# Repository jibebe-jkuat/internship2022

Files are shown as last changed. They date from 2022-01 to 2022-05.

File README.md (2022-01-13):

# EV project internship 2022

[PPT Slide](https://docs.google.com/presentation/d/1OYJdxiVj7QEA71lRJihHxvrTG2KooOGciBFLIxmFiqk/edit?usp=sharing)
(https://docs.google.com/presentation/d/1OYJdxiVj7QEA71lRJihHxvrTG2KooOGciBFLIxmFiqk/edit?usp=sharing)

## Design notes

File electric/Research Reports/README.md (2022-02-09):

# Contents

**1. Choice of Battery and Motor for Tricycle** - This document focuses on the calculations and
specifications used in determinig the final choice of the motor <br>

**2. Tractor Motor Sizing** - This document focuses on the calculations required for motor to be
used in the Shujaa Tractor. <br>

**3. Torque Calculations** -  This document focuses on the calculations required for torque required
 in the Shujaa Tractor.

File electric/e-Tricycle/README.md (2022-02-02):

# System Specifications

# MOTOR
Motor: BLDC <BR>
Voltage: 48V <br>
Power rating: 1200W <br>
Serial No: TP48V 1200W H60 210918 0001 <br>

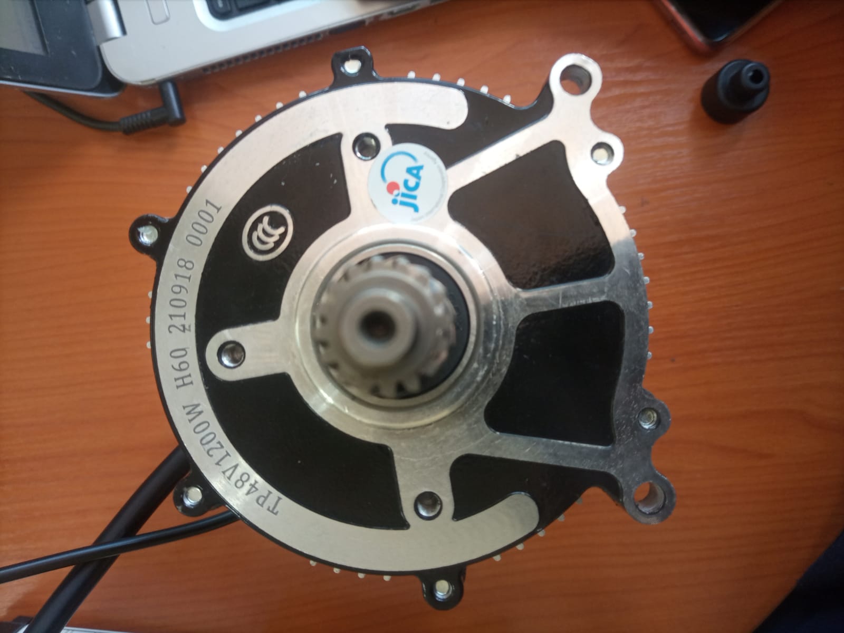
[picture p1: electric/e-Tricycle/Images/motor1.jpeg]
Motor 1

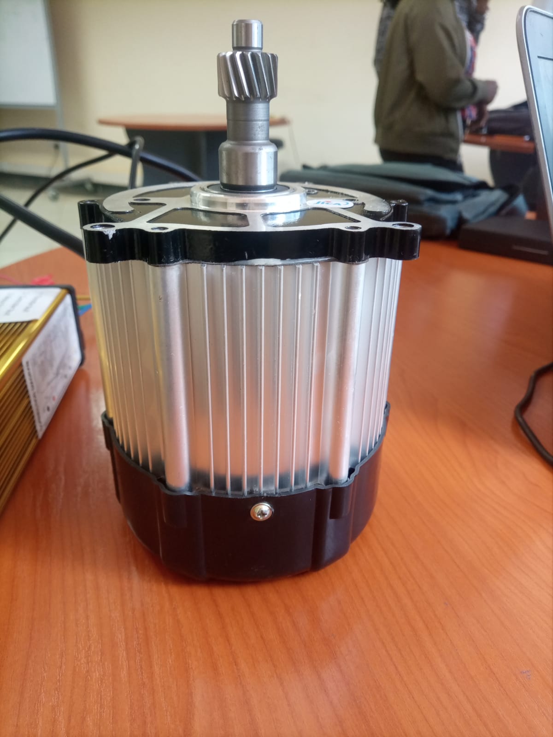
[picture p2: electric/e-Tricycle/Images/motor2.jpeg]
Motor 2


# Speed Controller

Voltage : 48V
Power rating: 1200W

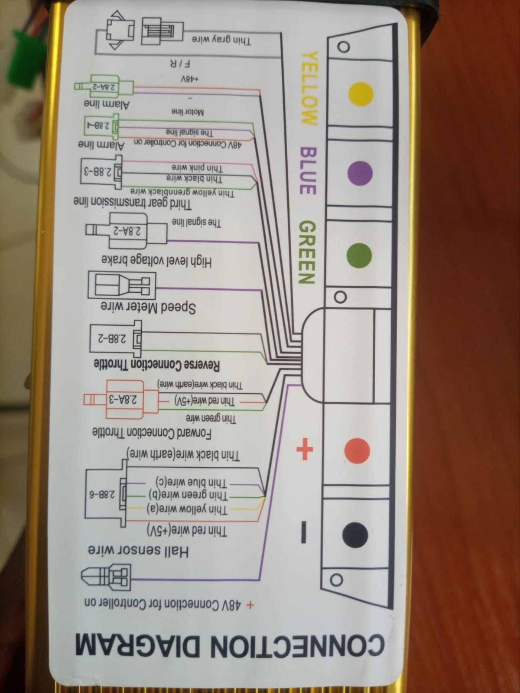
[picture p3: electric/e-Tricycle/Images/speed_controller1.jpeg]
Speed Controller 1

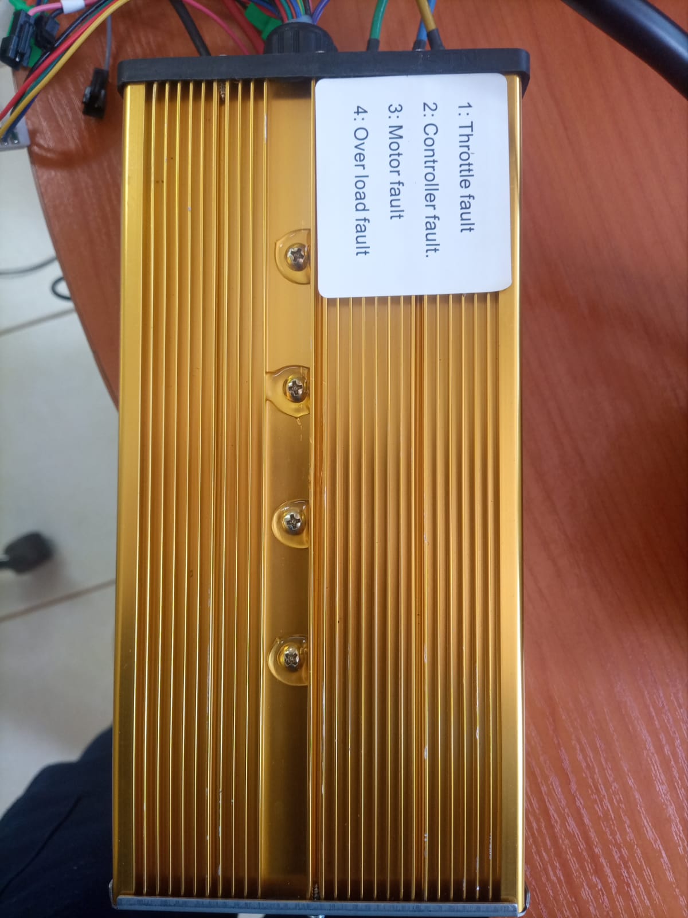
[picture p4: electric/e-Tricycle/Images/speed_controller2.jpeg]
Speed Controller 2

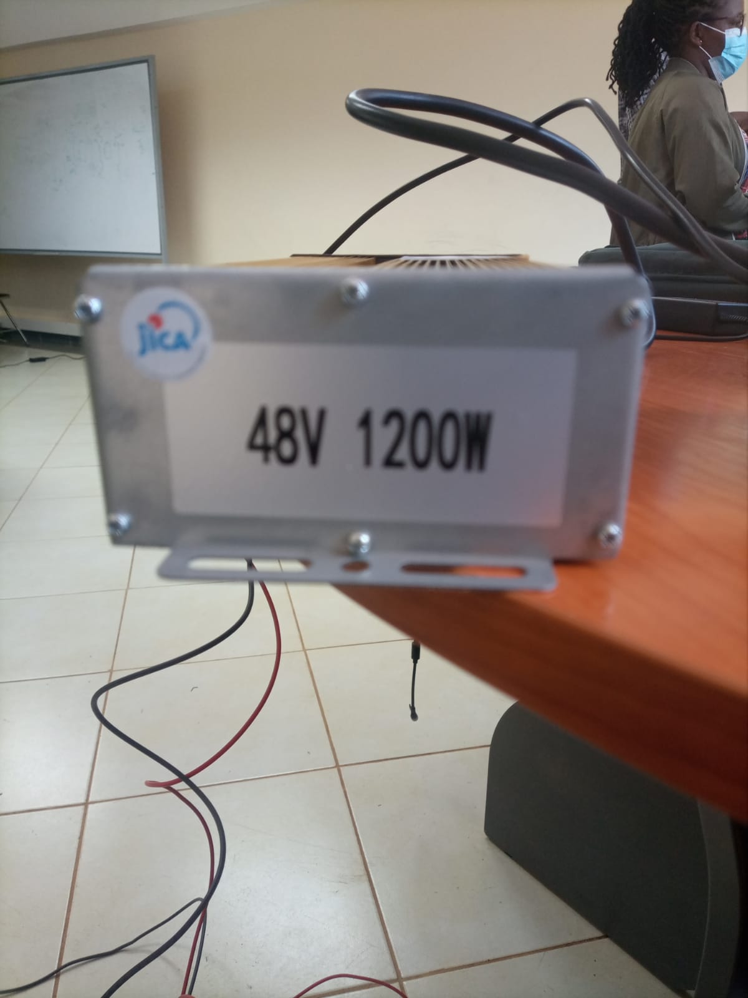
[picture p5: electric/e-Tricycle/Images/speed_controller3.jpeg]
Speed Controller 3

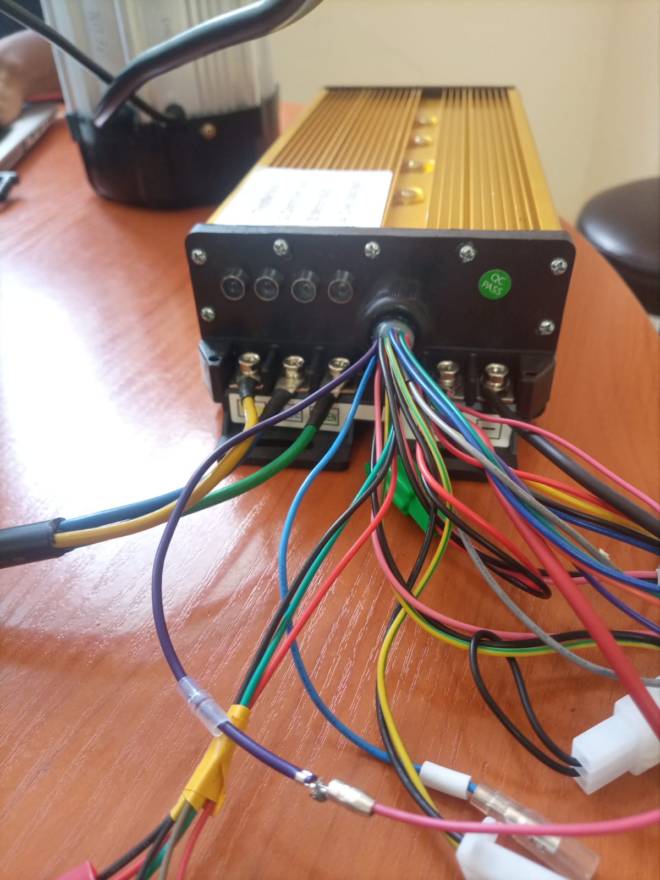
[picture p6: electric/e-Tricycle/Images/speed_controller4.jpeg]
Speed Controller 4


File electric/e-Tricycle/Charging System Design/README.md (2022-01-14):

## Charging System Design

Handles the design of a system to recharge batteries used in the tricycle and the shujaa tractor.

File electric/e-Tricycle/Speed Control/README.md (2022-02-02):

## Speed Control

Involves design of mechanisms to allow for control of the speed of the motor.
Schematics and final designs handled here.

## Design
In this implementation we will control the brushless motor using Arduino and ESC.

## Components

Brushless Motor <br>
ESC 30A <br>
Li-Po battery <br>
Arduino Board <br>
Potentiometer <br>
Breadboard and Jump Wires<br>

## Schematic
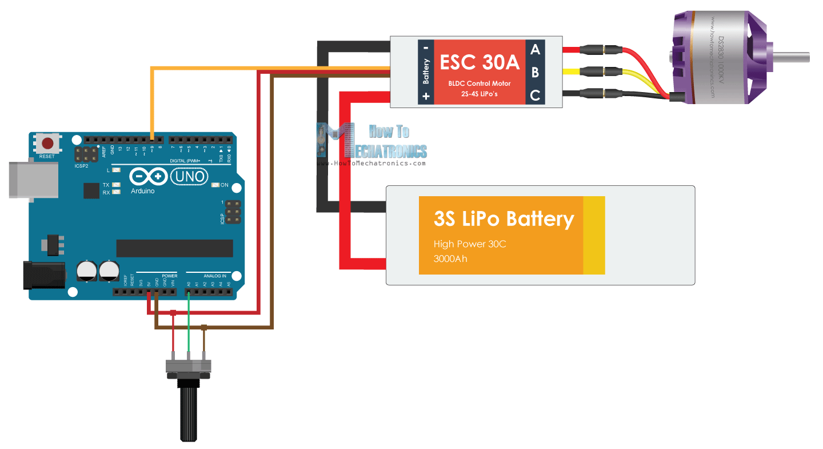
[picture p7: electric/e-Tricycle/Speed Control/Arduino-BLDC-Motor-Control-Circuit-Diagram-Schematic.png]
Circuit Schematic


# Alternative solution
This involves the use of a ready made Handlebar Throttle Switch to allow for the control of speed.

## Reasons for choosing this solution
Pairs well with the motor controller being used.( A plug and play solution). <br>
Has inbuilt LED speed display eliminating the need of an external LCD display. <br>
Does not involve the use of a microcontroller thus saving costs..

## Images of the Handlebar Throttle Switch
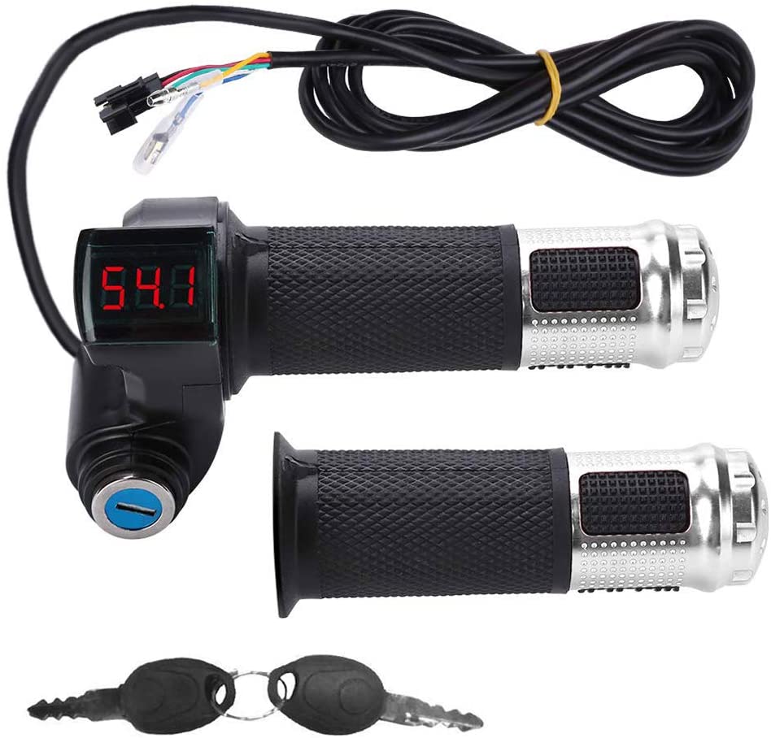
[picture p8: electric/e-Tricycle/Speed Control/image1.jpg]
Throttle Image 1

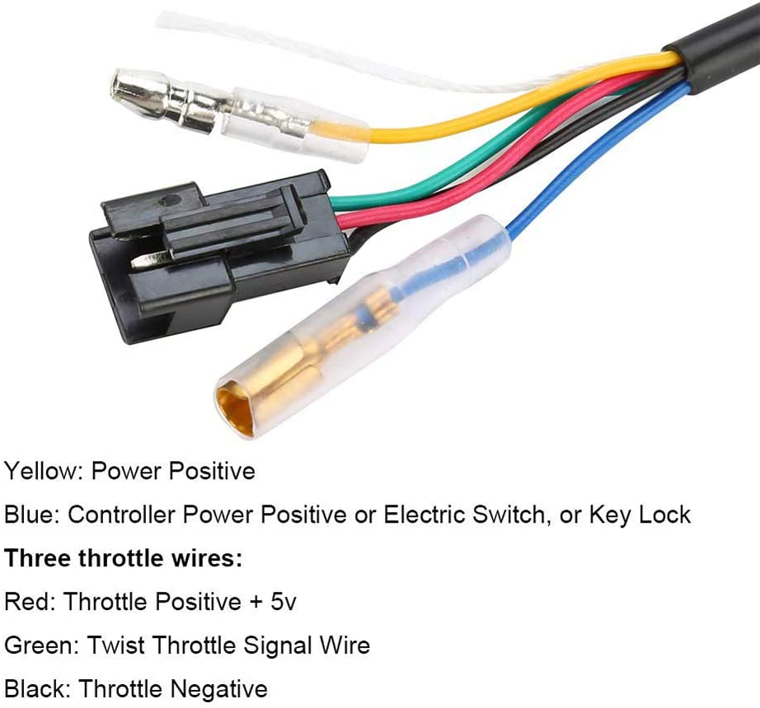
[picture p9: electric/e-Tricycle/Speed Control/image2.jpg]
Throttle Image 2

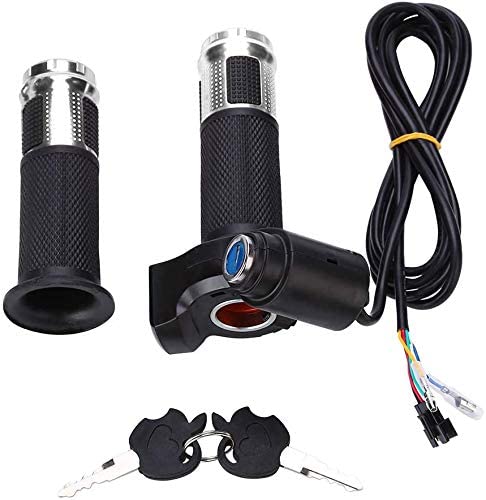
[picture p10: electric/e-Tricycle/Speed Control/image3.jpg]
Throttle Image 3


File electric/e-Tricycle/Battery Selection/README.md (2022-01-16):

## Handles the selection of the battery to be used for the tricycle.

Comparison of various types of batteries is done here.
The calculations and criteria for selection are also defined here.

## Specifications

| Specification | Value |
| --- | --- |
| Mass of motor | |
| Maximum passenger mass  |  |
| Mass of vehicle  |  |
| Mass of batteries |  |
| Total mass |  |
| Motor | BLDC |
| Voltage rating of motor  | 48V  |
| Power rating of motor  | 1800W  |
| Desired range | 100Km |
| Desired top speed | 35 km/h  |

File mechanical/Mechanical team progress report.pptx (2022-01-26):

## Internship 2022 Progress report on E-tricycle Name: Brian Muindi

## Internship 2022 Progress report on E-tricycle Name: Brian Muindi

## Tasks completed last week

- [#Github issue 11]Mechanism for starting motor

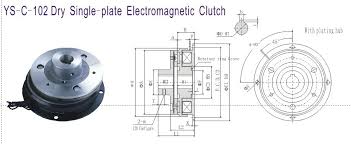
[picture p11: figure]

Why select the electromagnetic clutch?
- High precision torque control
- Superior durability and long life
- Stable slip torque

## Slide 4

- [#Github issue 19]3D modelling of the tricycle

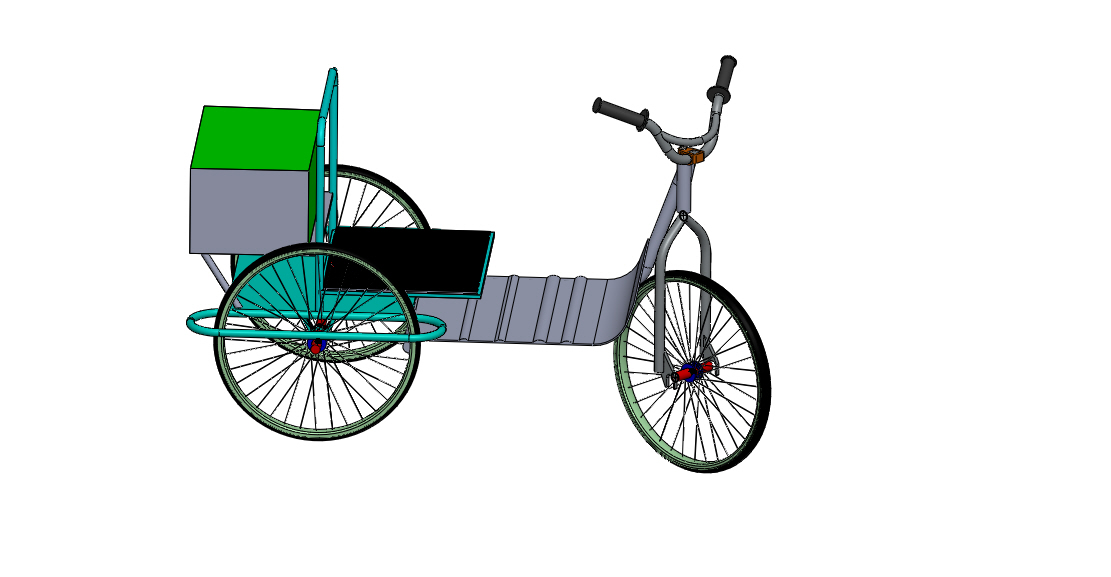
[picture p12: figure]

Parts redesigned
- Steering
- Braking mechanism
- Rear wheels
- Motor positioning

## Tasks in this week

- [#Github issue number 20] Shaft design

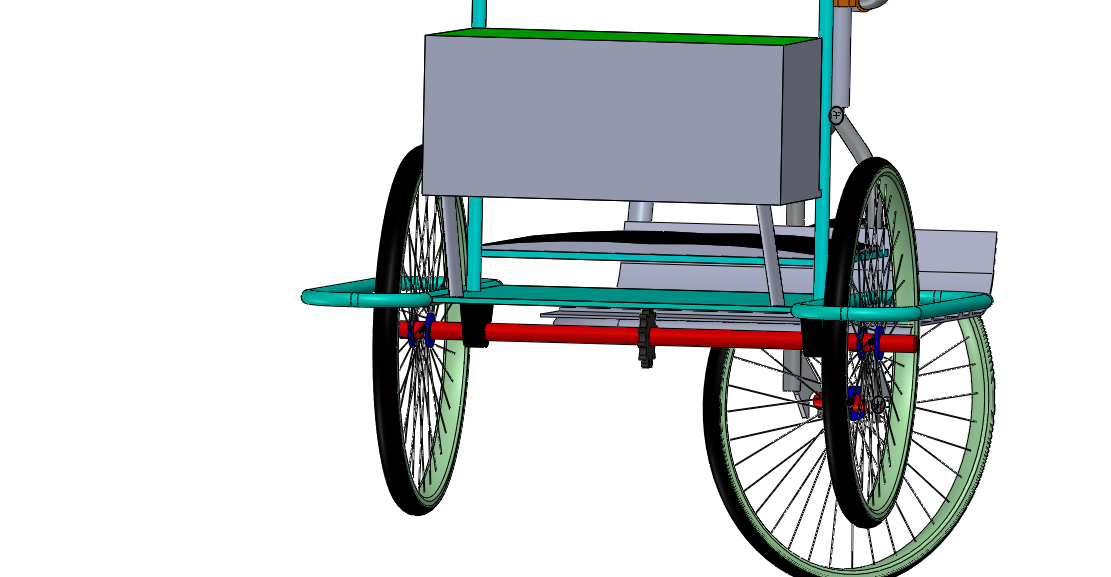
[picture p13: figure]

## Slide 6

- [#Github issue number 21] Design of chain drive

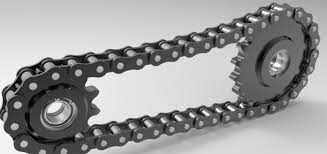
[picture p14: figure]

- No of teeth on sprockets
- Length of chain

## Timeline

Month | Intern week | Tasks
Jan
| Week 1 | Taking measurements and 3D modelling of the tricycle Mechanism for starting the motor Identification of parts
| Week 2 | Design of chain drive Shaft design Acquisition of parts
| Week 3
Feb | Week 4
| Week 5
| Week 6
| Week 7

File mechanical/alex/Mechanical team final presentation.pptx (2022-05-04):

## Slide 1

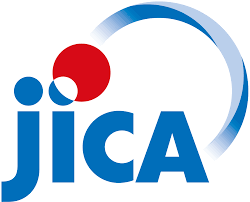
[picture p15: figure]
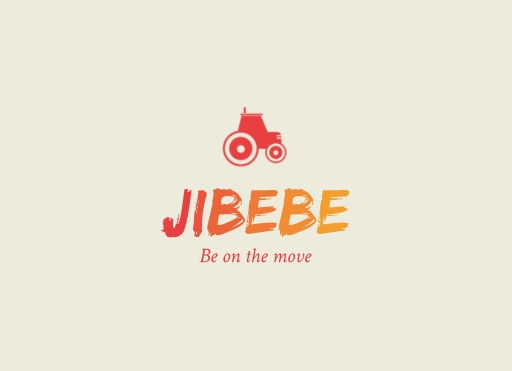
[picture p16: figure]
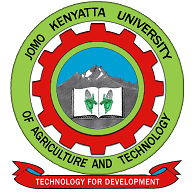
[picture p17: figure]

JIBEBE:ELECTRIC VEHICLE PROJECT

Supervisors : Dr Shohei Aoki
Mr Kipkorir Rono
Mr Joseph Kimani

Mechanical Team

Alex Mburu

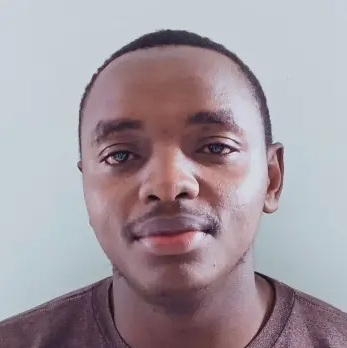
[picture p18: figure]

Emmanuel Njenga

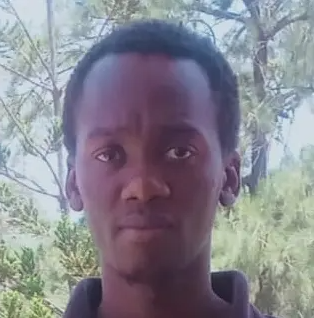
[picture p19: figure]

Peter Nzioki

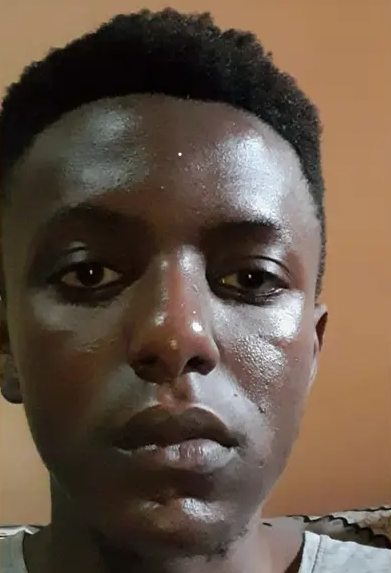
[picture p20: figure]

Brian Muindi

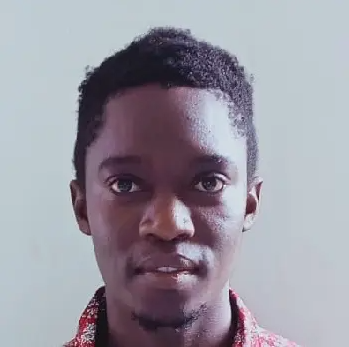
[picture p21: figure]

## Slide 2

INTRODUCTION

HUMAN POWERED TRICYCLE

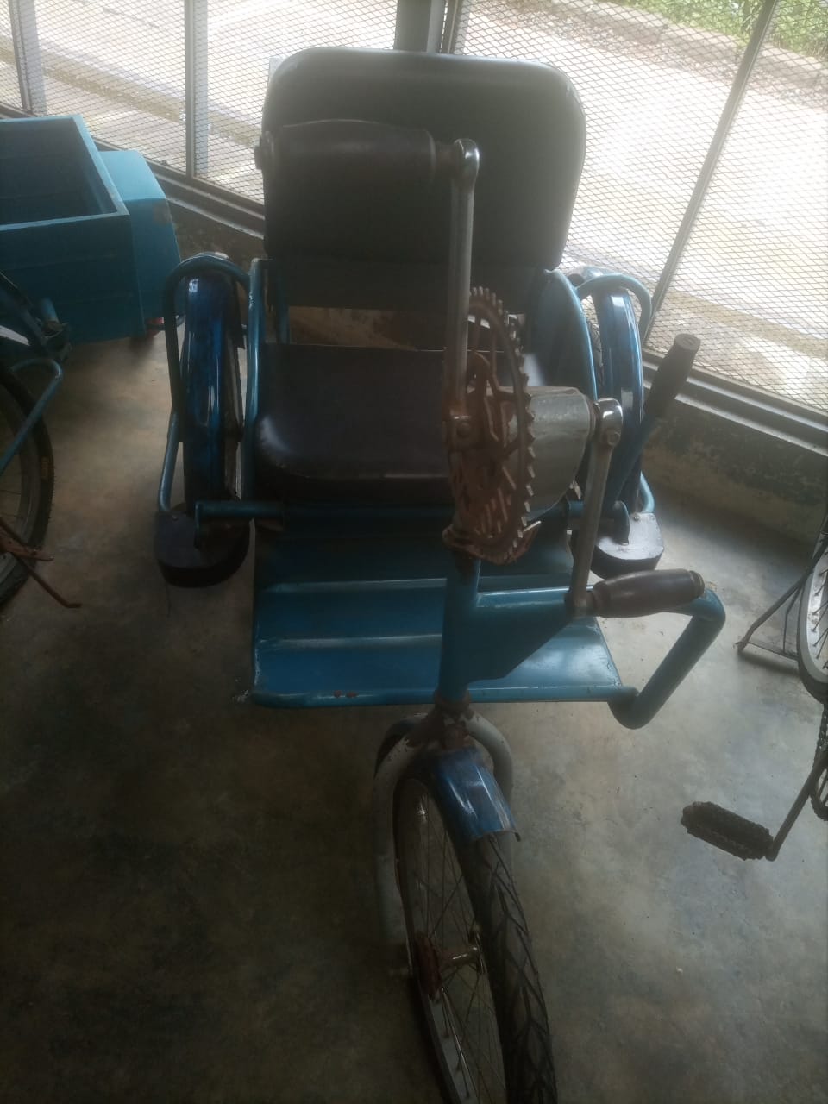
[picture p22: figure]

Specifications
- Human powered tricycle
- Rubber brake shoes-operated by a brake lever

Limitations
- Tedious
- Ineffective brake system

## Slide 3

E-Tricycle

Main Objective
Design fabrication and testing of an electric tricycle
Specific objectives
i. Determine the power requirements for the e-tricycle
ii. Design and fabricate the drive train
iii. Implement mechanical disc brakes

## Key Content Activities

- Power requirements-max speed of 16km/h-1200W-BLDC Motor
- Drive train

Design of rear axle
At 600rpm for the 1200W , T_(max) =19.10Nm
Using the maximum shear stress theory (Guest’s theory)
√(M^2 +T^2) = π/16×τ_(max) ×d^3
Diameter= 15.62mm

Chain drive design
- Design for the sprockets
Speed ratio=3.5
The larger sprocket=47T
Smaller sprocket = 15T
- Design for the chain
D=180mm
d=70mm
Center distance ,x = 170mm
Chain length= π(R+r)+2x+((R−r)/X)^2
L=760mm

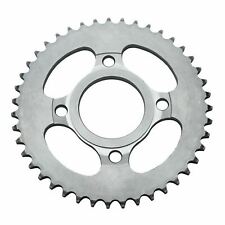
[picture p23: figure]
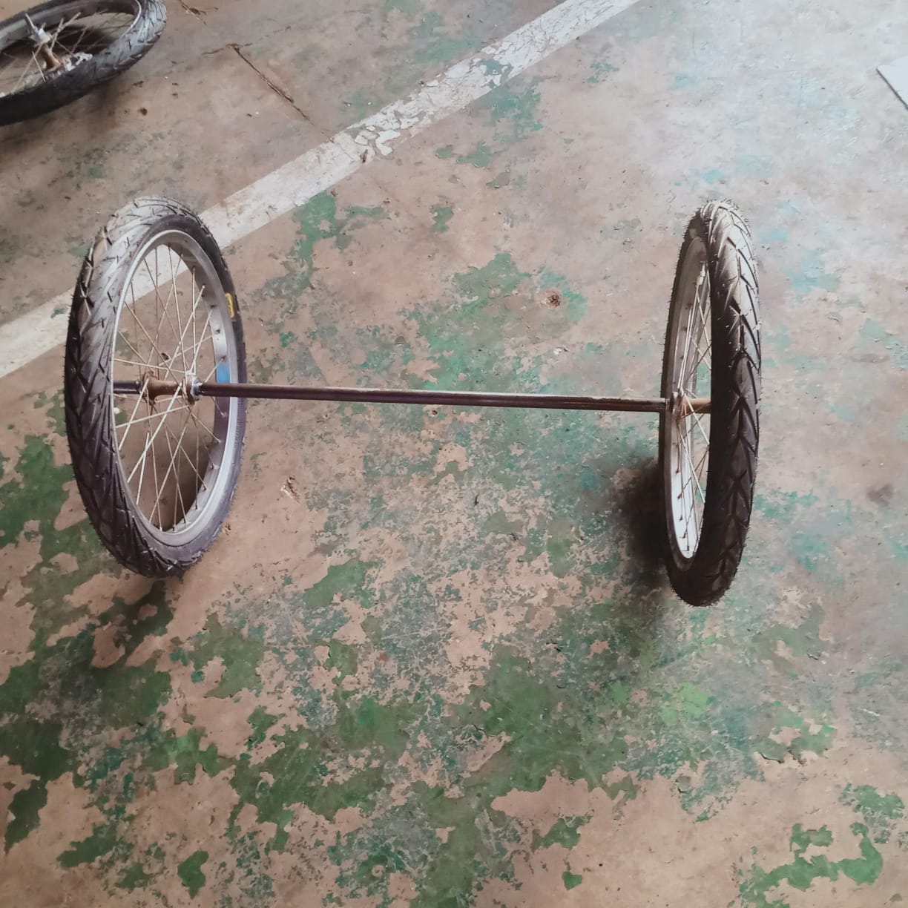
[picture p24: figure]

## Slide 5

3D modeling of the tricycle


Parts redesigned
- Steering
- Braking mechanism
- Rear wheels
- Motor positioning

Motor

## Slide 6

Fabrication and assembly of components

1.Steering-handle bars –
easy steering and other attachments i.e throttle,brake shifters

2.Braking mechanism
Mechanical brakes-both front and rear


Brake shifters


Rear Brake
rotor


Brake calipers

Front Brake
rotor

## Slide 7

Large sprocket

Drive train


BLDC motor

Chain


Motor


Attachment on the motor


Chain

Sprocket

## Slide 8

Assembly and testing of the e-tricycle

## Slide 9

Recommendations

1. Implement a suspension system for better ride comfort
2. Centre alignment of the handle bars to improve steering and better handling

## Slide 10

E-TRACTOR

Main Objective
Design fabrication and testing of an electric tractor
Specific objectives
i. Determine the power requirements for the e-shujaa tractor
ii. Stress and vibrational analysis of the e-tractor chassis
iii. Redesign the transmission system
iv. Assembly and testing of the e-tractor

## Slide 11

POWER REQUIREMENTS FOR THE SHUJAA E-TRACTOR

Case 1:Working mode
Power required when the tractor is accelerating(0-11km/h) and ploughing= 6.7923 kw

Case 2:Transport mode
Power required when the tractor is accelerating(0-30km/h) but NOT ploughing= 6.855kW

TORQUE REQUIREMENTS FOR THE SHUJAA E-TRACTOR

Case 1:Working mode
Working speed=11km/h
Torque from motor=27.28Nm
Torque required at the driving wheels=1800Nm

Gear ratio=47.98

Case 2:Transport mode
Working speed=30km/h
Torque from motor=27.28Nm
Torque required at the driving wheels=479.98Nm

15kW motor

Gear ratio=17.59

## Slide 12

Static and vibration analysis of the tractor chassis

Static analysis


Frequency analysis

Freq No | Rad/sec | Hertz
1 | 2986.7 | 475.34
2 | 5540.9 | 881.86
3 | 11383 | 1811.7
4 | 13137 | 2090.9
5 | 13327 | 2121.1

For a top speed of 3500rpm
Operating frequency of the motor is 58.33Hz (366.52rad/s)

FOS=15

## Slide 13

Thank you


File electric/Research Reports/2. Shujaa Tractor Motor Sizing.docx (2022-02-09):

JIBEBE

ELECTRICAL SUBSYSTEM

# MOTOR SIZING Calculations for Shujaa Tractor Motor

___

Placeholder image

# INTRODUCTION

This document will focus on the sizing of the motor to be used for the Shujaa Tractor. Proper sizing of a motor requires that 3 criteria must be met: torque, load inertia, and speed.

## A. Considering Tilling only

## Torque

This is defined as rotational force at a distance from the rotational axis. It is measured by units such as lb-in (pounds inch) in imperial or Nm (newton meter) in metric. Torque is just as important, if not more important, than the horsepower of a motor. Horsepower is how fast the work can be done and is calculated with torque multiplied by speed. In other words, torque is the capacity to do the work, and power is the speed at which the work can be done.

## Load Torque

Torque has 2 main components: load torque and acceleration torque. Load torque is the amount of torque constantly required for application and includes friction load and gravitational load. Acceleration torque is the torque required just for the maximum acceleration and deceleration rate for the load. The faster the load needs to accelerate, the higher the acceleration torque is. Sometimes the load torque is higher; sometimes the acceleration torque could be higher.

### 1. Lorem ipsum

Lorem ipsum dolor sit amet, consectetuer adipiscing elit, sed diam nonummy nibh euismod tincidunt ut laoreet dolore magna aliquam erat volutpat. Ut wisi enim ad minim veniam, quis nostrud exerci tation ullamcorper suscipit lobortis nisl ut aliquip ex ea commodo consequat.

### 2. Dolor sit amet

Duis autem vel eum iriure dolor in hendrerit in vulputate velit esse molestie consequat, vel illum dolore eu feugiat nulla facilisis at vero eros et accumsan.

## B. Considering Movement only

.For deciding the power rating of a vehicle, the vehicle dynamics like rolling resistance, gradient resistance, aerodynamic drag, etc. have to be considered. For illustration procedure for selecting

motor rating for an electric car of gross weight 450 kg is considered.

The force required for driving a vehicle is calculated below [1]-[4]:

Ftotal=Frolling+Fgradient+Faerodynamic drag (1)

Where, Ftotal =Total force

Frolling= force due to Rolling Resistance

Fgradient resistance= force due to Gradient Resistance

Faerodynamic drag=force due to aerodynamic drag

Ftotal is the total tractive force that the output of motor must overcome, in order to move the vehicle.

### A. ROLLING RESISTANCE

Rolling resistance is the resistance offered to the vehicle due to the contact of tires with road. The formula for calculating force due to rolling resistance is given by equation (2):

Frolling=Crr*M*g (2)

Where, Crr= coefficient of rolling resistance

M= mass in kg

g= acceleration due to gravity= 9.81 m/s²

Reference for Crr

Car tire on concrete: 0.010 to 0.015 , Steel on steel: 0.02 , Steel on wood: 0.22

Car tire on tar or asphalt: 0.030 to 0.035 , Aluminum on steel: 0.10 to 0.15

For the application considered, i.e a farm , choose rolling resistance to be 0.09 .

This paper (https://www.cambridge.org/core/services/aop-cambridge-core/content/view/ECD7544F00543D596B2D0EB3DD639516/S2633776220000758a.pdf/rolling-resistance-of-atv-tyre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) has values for rolling resistance in agriculture.

Crr=0.09 M= 450 kg, g = 9.81

Therefore,

Frolling= Crr*M*g

Power required to overcome the rolling resistance is:

Prolling= Frolling*V/3600 (3)

Where, V=velocity in kmph.

### B. GRADIENT RESISTANCE

Gradient resistance of the vehicle is the resistance offered to the vehicle while climbing a hill or flyover or while travelling in a downward slope.

The angle between the ground and slope of the path is represented as α, which is shown in the Figure below.


Figure: Angle between the ground and slope of a path

The formula for calculating the gradient resistance is given by equation (4):

Fgradient resistance=+ M*g*sin α (4)

In this illustration, let us consider the electric tractor runs on a flat road. Therefore, the angle α =0⁰

### C. AERODYNAMIC DRAG

Aerodynamic drag is the resistive force offered due to viscous force acting on the vehicle. It is largely determined by the shape of the vehicle.

The formula for ca lculating the aerodynamic drag is given by equation (5):

Faerodynamic drag= 0.5*CA*Af*ρ*(V+Vo)² (5)

These are the three main forces which act on the vehicle when it travels at constant speed. While accelerating and decelerating the effect of force due to inertia also acts. In this section, let us consider the power required to overcome Aerodynamic drag and other resistive forces to be around 1.3 kW.

### D. EFFIENCY

The total Power can then be calculated from the addition of the three powers above.

But electric motor with output power rating above should not be selected. The losses due transmission of power to the wheel must be included.

Therefore, the mechanical power output (Mtractive) required to drive the vehicle is given by equation (6):

Mtractive = Ptotal / η (6)

Where, η= efficiency of the transmission gear system.

Let us consider the efficiency of the transmission system to be 0.85.

Therefore the mechanical power output required can be calculated and appropriate motor can be selected.

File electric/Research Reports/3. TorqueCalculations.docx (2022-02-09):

Calculations To Determine The Maximum Torque To Be Produced By The Motor

The expected maximum load given acceleration of 0.5m/s² and a carriage of 220Kg is is 500W. To determine the maximum torque required for this application, then:

P=τω

ω=(2πn)/60

Smaller Sprocket: 48.42mm

Larger sprocket: 17.5cm

Wheel: 50cm

C = 2πr = πd

Diameter of wheel = 0.5m

Cof wheel = π x 0.5=0.5π m

Distance (D) covered by the wheel is 0.5π m/rev

The maximum speed of the tricycle is 4.5 m/s

Therefore, to obtain the number of revolutions per second for the wheel at maximum speed:

Speed in rps = ((4.5m)/s)/(0⋅5πm/(rⅇv))=9/π rev/s = 9/πrps

In rpm = 9/π x 60= 540/πrpm= 171.8873385 rpm

Method 1:

Large Sprocket Parameters:

Since angular velocity is the same for two axially connected wheels, then the rpm of the wheel is the same as the rpm of the large sprocket:

Rpm of wheel = 540/πrpm

C = 2πr = πd

Diameter of large sprocket = 0.175m

Cof wheel = π x 0.175m=0.175π m

Distance (D) covered by the larger sprocket is 0.175π m/rev

Linear speed of larger sprocket = 540/πrev/min x 0.175π m/rev = 94.5 m/min = 1.575 m/s

Small Sprocket parameters:

Since linear velocity is the same for two radially connected wheels, then the linear velocity of the large sprocket is the same as the linear velocity of the small sprocket:

V of small sprocket = 1.575 m/s

C = 2πr = πd

Diameter of small sprocket = 0.04842m

Cof small sprocket = π x 0.04842=0.04842π m

Distance (D) covered by the small sprocket is 0.04842π m/rev

Speed in rps = ((1.575m)/s)/(0⋅04842πm/(rⅇv))=8750/(269 π) rev/s = 8750/(269 π)rps

In rpm = = 8750/(269 π) x 60= 621.2367667 rpm

P=τω

ω=(2πn)/60

ω=(2π x 621.2367667)/60=65.05576208 rad/s

τ=P/ω= 500/65.05576208=7.685714286 nm

Method 2:

Large Sprocket Parameters:

Since angular velocity is the same for two axially connected wheels, then the rpm of the wheel is the same as the rpm of the large sprocket:

ω=(2πn)/60

ω=(2π x 540/π)/60

ω=(2πn)/60=18 rad/s

And r of the larger sprocket is 0.0875m

v=rω=0.0875 x 18=1.575 m/s

Small Sprocket parameters:

Since linear velocity is the same for two radially connected wheels, then the linear velocity of the large sprocket is the same as the linear velocity of the small sprocket:

V of small sprocket = 1.575 m/s

Radius = 0.02421m

ω=v/r

ω=1.575/0.02421=65.05576208 rad/s

τ=P/ω= 500/65.05576208=7.685714286 nm

On a flat surface, the expected torque at maximum speed is approximately 8 nm.

However, if the angular velocity was to fall due to motion on an inclined plane, i.e. a ramp, then the torque would dramatically increase. Let us take a critical case where the angular velocity dropped to 5 rad/s.

P=τω

τ=P/ω= 500/5=100 nm

Our BLDC motor is rated for an adjustable maximum torque between 120nm to 320nm hence it is safe above an angular velocity of:

ω=P/τ= 500/320=1.5625 rad/s

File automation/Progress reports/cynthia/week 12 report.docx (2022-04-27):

Internship 2022

# Progress report format for team meeting

Name: CYNTHIA KEMBOI

## Tasks completed last week

- [#83] GPS and Raspberry Pi

The raspberry pi’s OS was configured to be able to communicate with the GPS receiver. The circuit and the data collected are as shown below;


Figure 1 raspberry pi and GPS


Figure 2 data collected


Figure 3 position of our raspberry pi

- [#87] Raspberry Pi and Compass

Magnetometer HMC5883L is used for measuring the direction and magnitude of the Earth’s magnetic field. It is used for low-cost compassing and magnetometry. It measures the Earth’s magnetic field value along the X, Y and Z axes from milli-gauss to 8 gauss. It can be used to find the direction of heading of the device. It uses I2C protocol for communication with microcontroller.

After initialization, X,Y AND Z-axis registers raw values, The head value is calculated using the following formulae:

Magnetic heading=atan2(y/x) (radian)

True heading=Magnetic heading+Declination Angle (Radian)


Figure 4 raspberry pi and compass


Figure 5 compass detected

## Navit

Navit is a car navigation system with routing engine. Navit's modular design is capable of using vector maps of various formats for routing and rendering on the screen. It's even possible to use multiple maps at the same time. The GTK+ or SDL user interfaces are designed to work well with touch screen displays. Points of Interest of various formats are displayed on the map. The current vehicle position is either read from gpsd or directly from NMEA GPS sensors. The routing engine not only calculates an optimal route to your destination, but also generates directions and even speaks to you using espeak. Navit currently speaks 49 languages, can run on various platforms (Linux, Windows, Android, OpenMoko Freerunner, Wince, Nokia n800 Internet tables, iPhone, Zaurus..)

## Tasks in this week

- [#88] Raspberry Pi and Navit

# Timeline

Month | Intern week | Tasks
Jan
| Week 1 | Identification of parts and drawing of the chassis diagram.
| Week 2 | Circuit diagram and acquisition of parts.
| Week 3 | Definition of the path to be followed by the robot car. Laser cutting of the parts.

Feb | Week 4 | - Assembly of the robot - Ultrasonic program implementation
| Week 5 | - GPS and compass navigation - Path definition
| Week 6 | Object identification using computer vision. (Raspberry pi & camera)
| Week 7 | Transmission of live feed and data from the robot (transmitter and receiver)
| Week 8 | Object dection (static and dynamic)

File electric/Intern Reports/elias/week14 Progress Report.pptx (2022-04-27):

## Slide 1

JIBEBE INTERNSHIP 2022


WEEKLY REPORT: ELIAS CHERUIYOT

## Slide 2

[#96] Eliminating inconsistency of motor speeds- The team managed to smoothen out inconsistency of speeds of the motor by introducing a 100uF capacitor on the linear acceleration circuit.
[#97]Incorporating reverse function in e-tricycle- The team managed to come up with a circuit that Incorporating reverse function. Circuit which has
1. Button for reverse direction.
2. Large LED/Industrial LED to indicate reverse is engaged.
3. Buzzer to also indicate reverse is engaged


TASKS COMPLETED LAST WEEK


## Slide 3


## TASKS THIS WEEK

- [#84] PCB drawing and fabrication-

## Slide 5


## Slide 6

Thank You

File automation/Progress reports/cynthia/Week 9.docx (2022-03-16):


Internship 2022 Progress report

Name: Cynthia Kemboi

# Tasks completed last week

- [#71] Tillage and automation.

Development of guidance systems and autonomous vehicles is current state-of-the-art in agricultural mechanization. Since the late nineteenth century, farmers have been devising methods of making a tractor follow a plough furrow by using a feeler. In the later part of the twentieth century, the combination of hydraulics and electronics allowed for more sophisticated guidance strategies. These strategies include low force feelers that can guide the tractor or implement based on the position or rows, and guiding the tractor based on the position of the vehicle from the Global Positioning System (GPS).

Using a guidance system for agricultural machinery is not a new concept. One of the earliest guidance systems used a wheel to steer a steam-powered traction engine along a plow furrow. A small steel wheel was designed to run in a plow furrow next to the tractor. The guidance wheel was attached to the front wheels of the tractor and held up against the furrow using a spring. As the tractor veered left or right, the guidance wheel in the furrow would steer the tractor in the opposite direction, keeping it on track parallel to the plow furrow.


Figure showing an early furrow following guidance system

Depending on the situation, different guidance strategies or groups of guidance strategies may be needed to achieve the best outcome. Each strategy uses or combines various technologies to guide the vehicle. For example, consider a tractor cultivating a row crop, such as cotton. A sensor with feelers can locate the row accurately, and ensure that the vehicle follows the row. However, there is no assurance that the tractor is cultivating the correct set of rows. The GPS system can locate the tractor on the proper set of rows, but the accuracy may not be precise enough to cultivate between the rows without damaging the crop. The two systems may be combined to provide a better solution. The ECU can use the GPS portion of the guidance system to ensure that the tractor is cultivating the correct set of rows then switch to the feeler guidance system to ensure that the cultivator is accurately operating between the rows, minimizing the damage to the crops.


A guidance system that uses crop feelers

There are four guidance strategies:

1. Manual—an operator steers the vehicle based on their observations of the surroundings.
2. Operator assisted—an operator steers the vehicle based on a signal from the guidance system.
3. Semi-autonomous—the guidance system steers the vehicle, but an operator is present to ensure the system is working properly and perform other vehicle functions that are not automated.
4. Fully autonomous—no operator required! The benefits and challenges of each strategy are identified below


# Tasks in this week

● [#49] Computer vision (vehicle detection, static and dynamic objects )

# Timeline

Month | Intern week | Tasks
Jan
| Week 1 | Identification of parts and drawing of the chassis diagram.
| Week 2 | Circuit diagram and acquisition of parts.
| Week 3 | Definition of the path to be followed by the robot car. Laser cutting of the parts.

Feb | Week 4 | - Assembly of the robot - Ultrasonic program implementation
| Week 5 | - GPS and compass navigation - Path definition
| Week 6 | Object identification using computer vision. (Raspberry pi & camera)
| Week 7 | Transmission of live feed and data from the robot (transmitter and receiver)
| Week 8 | Object dection (static and dynamic)

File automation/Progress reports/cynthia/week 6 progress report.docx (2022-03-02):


Internship 2022 Progress report format

Name: CYNTHIA KEMBOI

# Tasks completed last week

## ● [#49] Computer Vision

Computer vision is a field of artificial intelligence (AI) that enables computers and systems to derive meaningful information from digital images, videos and other visual inputs, and take actions or make recommendations based on that information. If AI enables computers to think, computer vision enables them to see, observe and understand.

Computer vision works much the same as human vision, except humans have a head start. Human sight has the advantage of lifetimes of context to train how to tell objects apart, how far away they are, whether they are moving and whether there is something wrong in an image.

Computer vision trains machines to perform these functions, but it has to do it in much less time with cameras, data and algorithms rather than retinas, optic nerves and a visual cortex. Because a system trained to inspect products or watch a production asset can analyze thousands of products or processes a minute, noticing imperceptible defects or issues, it can quickly surpass human capabilities.

Applications

- Intruder detection
- Defect detection
- Metrology
- Assembly verification
- Screen reading
- CV plus robotics for bin picking

Computer vision with the Raspberry Pi

Computer Vision (CV) allows your Raspberry Pi to see things. In practical terms, this means that your Raspberry Pi can analyze an image, looking for items of interest and even recognizing faces and text.

If you link this with a camera to supply the images, then all sorts of possibilities open up.


The raspberry pi-based obstacle avoiding robot consists of three main modules i.e., camera module, raspberry pi, motor drivers. The camera module gets the input image which are obtained during real time operation. The raspberry pi is a platform consisting of all necessary hardware module assembled on it. It receives the images from the camera module. It carries out image processing and checks whether there are any obstacles in path of the robot and if any obstacle occurs then it will send the signal further to motor driver accordingly. The motor driver actually of two sub motors- left and right motor. These motors receive the signal from raspberry pi in case of any appearance if the obstacle in its path the motors work accordingly to signal and moves in left or right direction with the help of the left and right motor to avoid obstacles.


There are two versions of the Camera Module:

- The standard version (https://www.raspberrypi.org/products/camera-module-v2/), which is designed to take pictures in normal light
- The NoIR version, which doesn’t have an infrared filter, so you can use it together with an infrared light source to take pictures in the dark

# Tasks in this week

- [#50] object detection and identification
- [#51] raspberry pi and Arduino mega connection
- [#26] obstacle avoidance using computer vision

# Timeline

Month | Intern week | Tasks
Jan
| Week 1 | Identification of parts and drawing of the chassis diagram.
| Week 2 | Circuit diagram and acquisition of parts.
| Week 3 | Definition of the path to be followed by the robot car. Laser cutting of the parts.

Feb | Week 4 | - Assembly of the robot - Ultrasonic program implementation
| Week 5 | - GPS and compass navigation - Path definition


| Week 6 | Object identification using computer vision. (Raspberry pi & camera)
| Week 7 | Transmission of live feed and data from the robot (transmitter and receiver)
| Week 8 | Implementation of tillage program on the robot (gathering and casting).

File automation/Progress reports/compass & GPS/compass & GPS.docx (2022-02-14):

Compass

The HMC5883L sensor is a 3-axis digital magnetometer IC designed for low-field magnetic sensing. The sensor has a full-scale range of +8 to -8 Gauss and a resolution of up to 5 milli-Gauss. Communication with the HMC5883L is simple and all done through an I2C interface. That means you will need to connect power, ground and only two cables to Arduino Uno board (SDA, SCL).

The HMC5883L board can be powered up by 5V or 3.3V pins of Arduino Uno board. No need to add any capacitors or resistors to your circuit.

Pinout and connection with Uno:

- Vcc to 5V or 3.3V
- GND to GND
- SDA to A4
- SCL to A5
- DRDY to nothing...

Because this is a magnetic compass if you put it near to battery, motors, metallic surface or magnetic field, the result will diverge from the actual.

The HMC5883L utilizes Anisotropic Magneto resistive (AMR) technology that provides advantages over other magnetic sensor technologies. These anisotropic, directional sensors feature precision in-axis sensitivity and linearity. These sensors’ solid-state construction with very low cross-axis sensitivity is designed to measure both the direction and the magnitude of Earth’s magnetic fields, from milli-gauss to 8 gausses.


GPS

The Global Positioning System (GPS) is a satellite based navigation system that provides location and time information. The system is freely accessible to anyone with a GPS receiver and unobstructed line of sight to at least four of GPS satellites. A GPS receiver calculates its position by precisely timing the signals sent by GPS satellites.

GPS modules contain tiny processors and antennas that directly receive data sent by satellites through dedicated RF frequencies. From there, it’ll receive timestamp from each visible satellites, along with other pieces of data. If the module’s antenna can spot 4 or more satellites, it’s able to accurately calculate its position and time.

The four well-known Global Navigation Satellite System include GPS, BDS(Beidou), GLONASS and GALILEO four satellite navigation systems. The earliest appeared in the United States is GPS (Global Positioning System), which is the most complete technology at this stage. BDS, GLONASS and GALILEO have become the other largest satellite navigation systems in the world and are currently in the process of modernization.


Figure 1 satellite triangulation


Figure 2 GPS Expectations

The first stage of the autonomous guidance algorithm determined the angle difference by comparing the current heading to the target azimuth. This step allowed the robot to determine what direction (left or right) it should turn. The next step determined the distance between the robot location and the target location. The robot program continuously calculates the distance and the minimum turn required. When the heading angle is equal to the azimuth angle, the robot is steered towards the destination point. When the distance is equal to zero, the robot arrives at the destination point


Figure 3 Autonomous robot guidance algorithm

A waypoint is the term used to describe a reference point for robot navigation. It includes destination latitude and longitude data. In this study, waypoints stored previously in the database were used for point-to-point steering in autonomous robot guidance. Two important angles called heading and azimuth angles were used to steer the robot autonomously. The heading angle was an angle between North (true or magnetic) and the current direction of the longitudinal axis of a robot in the horizontal plane. It was continuously received from the GPS receiver by the robot program. The azimuth was an angle between North and the destination point. It was continuously calculated by the robot program with Harvesine equation.

The Haversine formula calculates the shortest distance between two points on a sphere using their latitudes and longitudes measured along the surface. It is important for use in navigation.

The haversine can be expressed in trigonometric function as:

haversine(θ)=sin^2 θ/2 The haversine of the central angle (which is d/r) is calculated by the following formula:

where r is the radius of the earth(6371 km), d is the distance between two points, is the latitude of the two points, and is the longitude of the two points respectively.
Solving d by applying the inverse haversine or by using the inverse sine function, we get:

or

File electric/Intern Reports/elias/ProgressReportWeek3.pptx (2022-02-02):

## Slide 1

Jibebe Internship 2022
Progress report
Electric team
Name: ELIAS CHERUIYOT

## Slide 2

Tasks completed last week

[#14] Electrical system experiment – The motor was appropriately connected to the controller which was in turn connected to a 53.7v rectifier which powered the system in place of the lithium battery that we are yet to acquire. This was necessary to determine the behaviour of the motor at start up. In place of the throttle switch that we are yet to receive we use a potentiometer to vary the voltage supplied to the bldc controller
[#13] Determination of required electric components – Brainstorming was done by the team and we were able to contact a number of suppliers of the items needed that includes Throttle switch and lithium battery
[#5]BLDC Motor Acquiring- We decided to go with the already available 1200W motor.

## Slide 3


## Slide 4

Tasks in this week

● [#4] Charge controller acquiring
● [#18]Analysis of performance curves
● [#30] Getting experimental characteristics of loading motor
● [#34] Determination of components for tractor and calculation of their values

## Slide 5

Timeline

Month | Intern Week | Tasks
Jan | Week 1 | Design of required Battery Pack for Motor and Speed Control
| Week 2 | Acquisition and procurement if required components
| Week 3 | Testing of components fir tricycle and design of tractor electric system
Feb | Week 4 | Integration of ordered parts to final tricycle implementation. Procurement of components for tractor
| Week 5 | Solving miscellaneous issues arising from tricycle. Testing of tractor components
| Week 6 | Testing of tractor components
| Week 7 | Integration of final electric system of tractor
| Week 8 | Integration with other subsystems

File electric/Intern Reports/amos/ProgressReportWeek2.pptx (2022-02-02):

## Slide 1

Jibebe Internship 2022
Progress report Week 2
Electric team
Name: Amos Wanene

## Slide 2

Tasks completed last week

[#11] Mechanism for starting motor – The electric team and the mechanical team were able to come up with the solution to the jerk start problem encountered due to the transients of starting a motor by employing an electromagnetic clutch which would be responsible for coupling the motor to the load once it achieved steady state operation.
[#12] Simulation of motor operation – Simulation of the entire electric system; motor, battery and the projected load, was done in order to understand the various characteristics of the motor.

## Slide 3

In the graphs below, the motor simulation is done with the following conditions:
i. The battery specifications are at 48V 50Ah Li-ion battery
ii. All curves are plotted at maximum motor speed, i.e. 16km/hr.
iii. The load of the tricycle is 150kg
iv. The human power is 0W which indicates that no work is done by the passenger. All the work is done by the motor, i.e. it is fully electric.
Of importance in the following curves is to observe that as the grade value (gradient) is increased, the power required to maintain a speed of 16km/hr increases. In the first graph, with a grade of 0%, the motor power is 85W. In the second graph, with a grade of 2.5%, the motor power is 247W. In the third graph, with a grade of 5%, the motor power is 409W.

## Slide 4


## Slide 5


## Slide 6


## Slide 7

Tasks in this week

● [#14] Electric system experiments
● [#18] Analysis of perfomance curves

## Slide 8

Timeline

Month | Intern Week | Tasks
Jan | Week 1 | Design of required Battery Pack for Motor and Speed Control
| Week 2 | Acquisition and procurement if required components
| Week 3 | Testing of components fir tricycle and design of tractor electric system
Feb | Week 4 | Integration of ordered parts to final tricycle implementation. Procurement of components for tractor
| Week 5 | Solving miscellaneous issues arising from tricycle. Testing of tractor components
| Week 6 | Testing of tractor components
| Week 7 | Integration of final electric system of tractor
| Week 8 | Integration with other subsystems

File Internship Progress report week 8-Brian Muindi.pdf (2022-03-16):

# Internship 2022


## Name: Brian Muindi

# Tasks completed last week

## ●[#55] Fabrication of the motor mounting


[#54] fabrication of motor shaft attachment

# Tasks in this week

## - [#31] Fabrication and Assembly of the tricycle - [#64] Acquisition of parts for the shujaa tractor - [#56]Design of the transmission system for the Shujaa tractor

# TIMELINE

Month | Intern week | Tasks
Jan | Week 1 Week 2 | Taking measurements and 3D modelling of the tricycle Identification of parts Design of chain drive Shaft design Disassembly of the tricycle
Feb | Week 3 | Acquisition of parts Fabrication of tricycle components Literature review on E-tractors
| Week 4 | Identification of parts to be replaced on the shujaa tractor Calculation of power requirements for the shujaa tractor Measurement of chassis

| Week 5 | Design of various transmission components 3D modeling of the Shujaa tractor
| Week 6 | Vibration and stress analysis Acquisition of parts for the tricycle
March | Week 7 | Design of the transmission system of shujaa tractor Fabrication of motor shaft attachment for the tricycle Fabrication of motor housing
| Week 8 | Final fabrication of parts for the tricycle Assembly of the E-tricycle Design and acquisition of the gearbox (shujaa tractor)

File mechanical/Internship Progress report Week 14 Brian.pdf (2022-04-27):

NAME: Brian Muindi


# Tasks completed last week

## [#91] Testing the E-tricycle (test ride around the workshop)

### Issues arising from the test:

### - Slip of the motor shaft coupling reducing the efficiency of transmission of the drive ✓ Creating a recess ( flattened area) on the motor shaft ✓ Increasing contact pressure generated by the grab screw


# Tasks in this week

### [#90] Aesthetic finishing of E-tricycle Painting of the tricycle requires disassembly of some components or covering them

## [#31] Assembly of the E-tricycle

### Further testing of the transmission system through test rides

# TIMELINE

Month | Intern week | Tasks
Jan | Week 1 Week 2 | Taking measurements and 3D modelling of the tricycle Identification of parts Design of chain drive Shaft design Disassembly of the tricycle
Feb | Week 3 | Acquisition of parts Fabrication of tricycle components Literature review on E-tractors

| Week 4 | Identification of parts to be replaced on the shujaa tractor Calculation of power requirements for the shujaa tractor Measurement of chassis
| Week 5 | Design of various transmission components 3D modeling of the Shujaa tractor
| Week 6 | Vibration and stress analysis Acquisition of parts for the tricycle
March | Week 7 | Design of the transmission system of shujaa tractor Fabrication of motor shaft attachment for the tricycle Fabrication of motor housing
| Week 8 | Final fabrication of parts for the tricycle Assembly of the E-tricycle Design and acquisition of the gearbox (shujaa tractor)

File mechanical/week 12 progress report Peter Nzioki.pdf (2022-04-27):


# INTERNSHIP 2022

NAME: PETER NZIOKI

# Tasks completed last week

## ●[#2] Sub-system fabrication and assembly

1. Motor coupling mounting
2. Motor housing mounting on the E-tricycle
3. Rear brake caliper mounting



# Tasks in this week

### - [#5] Aesthetic finishing of E-tricycle

✓ Cleaning welds, washing and painting

### - [#3] Final assembly of the E-tricycle - [#4] Further research into Shujaa tractor gearbox

✓ looking into viability of the existing unit in conjunction with an electromagnetic clutch system and electro-mechanical actuators as shifting mechanisms

# TIMELINE

Month | Intern week | Tasks
Jan | Week 1 Week 2 | Taking measurements and 3D modelling of the tricycle Identification of parts Design of chain drive Shaft design Disassembly of the tricycle

Feb | Week 3 | Acquisition of parts Fabrication of tricycle components Literature review on E-tractors
| Week 4 | Identification of parts to be replaced on the shujaa tractor Calculation of power requirements for the shujaa tractor Measurement of chassis
| Week 5 | Design of various transmission components 3D modeling of the Shujaa tractor
| Week 6 | Vibration and stress analysis Acquisition of parts for the tricycle
March | Week 7 | Design of the transmission system of shujaa tractor Fabrication of motor shaft attachment for the tricycle Fabrication of motor housing
| Week 8 | Final fabrication of parts for the tricycle Assembly of the E-tricycle Design and acquisition of the gearbox (shujaa tractor)

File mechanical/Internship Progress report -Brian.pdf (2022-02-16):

# Internship 2022

# Progress report on E-tricycle and Shujaa tractor

Name: Brian Muindi

## Tasks completed last week

[#32] Acquisition of parts

- Flange couplings


## Tasks completed last week

- [#31] Fabrication and assembly of E tricycle


## Tasks completed last week

- [#41]Identification of parts to be replaced on the Shujaa tractor (https://github.com/jibebe-jkuat/internship2022/issues/41)
- Fuel tank-battery pack
- Engine-motor
- Gearbox

## Tasks in this week

- [#40] Measurement of Shujaa Tractor chassis (https://github.com/jibebe-jkuat/internship2022/issues/40)


## Tasks in this week

- [#42] 3D modeling of the chassis (https://github.com/jibebe-jkuat/internship2022/issues/42)
- [#33] Calculation of power requirements for the Shujaaa tractor (https://github.com/jibebe-jkuat/internship2022/issues/33)
- [#48]Design of motor mounting and placement on the E-tricycle

## Timeline


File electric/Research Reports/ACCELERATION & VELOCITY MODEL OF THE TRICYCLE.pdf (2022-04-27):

ACCELERATION CONTROL

Since the design consideration was for 9s, the electric team used an RC circuit to apply the required delay.

An RC circuit induces a specified delay in a circuit by utilizing the charging principle of a capacitor. A capacitor charges to near full state in 5-time constants.

v = v0(1 − e

−t
RC)


Therefore, in order to design for a 9s charge delay, the time constant of the capacitor should be ¹
5

of the
required full delay.

τ = RC

τ =

Delay
5

=

9
5

= 1.8s

Let the capacitor value of the delay circuit be 220µF as it is a common capacitor value:

R =

τ
C

R =

1.8
220µF

= 8.1818181 kΩ

The closest standard resistor value is 8.2 kΩ


ACCELERATION MODEL OF THE TRICYCLE

v = v0(1 − e

−t
RC)

n ∝ v

n = kv

n = k x v0(1 − e

−t
RC)

Let k x v0 be n0

n = n0(1 − e

−t
RC)

ⅆs
ⅆt

= n0(1 − e

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
RC e

−t
RC

Power = Force × velocity

Power = mass x acceleration x velocity

Power= m × {

n0
RC

e

−t
RC } × {n0(1 − e

−t
RC)}

Where in our specific case:

v0 = 5V

k =

8
9
n0 = 4.4444444 m/s

τ = RC = 1.8s

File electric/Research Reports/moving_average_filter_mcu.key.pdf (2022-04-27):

## Implementation of digital moving average filter on microcontroller

## Acceleration/Deceleration circuit

- In acceleration control (e.g. CNC controller), acceleration/deceleration circuit is used to shape the velocity command
- There are three kinds of acceleration circuit

Acceleration/
Deceleration circuit

Position

Velocity

## 1) Exponential acceleration &

## deceleration


- This is equivalent to RC circuit you developed
- We are not using this one

## 2) Moving average acceleration

## (i.e. Linear acceleration)


- We use this one
- is the constant input
- is the time to complete acceleration (9 seconds in our case)

VFC
τ1

### 3) Two-stage moving average acceleration (i.e. S-curve acceleration)


- By chaining two moving average filters, the velocity profile becomes S-curve
- We don't use this one

Moving
average

Moving
average
Input | Output

## Let's calculate continuous transfer function G

← Gma; = Fout; (s)/Fin(s)

- Transfer function G(s) is calculated as
G(s) =

1
τ1

## 1 − e⁻τ1s

s

## Matlab simulation


tau1 = 9;
s = tf('s');
G = 1/tau1*(1-exp(-tau1*s))/s; step(G)

It is successfully accelerated in 9 seconds

## Discretize transfer function G to H

- We need to discretize transfer function to implement the algorithm on the microcontroller
- In Matlab, we can use c2d() function

tau1 = 9;
s = tf('s');
G = 1/tau1*(1-exp(-tau1*s))/s; sampling_time = 0.01;
H = c2d(G,sampling_time,'zoh'); step(H);

10 [ms]

Zero-Order Hold

## Check discrete step response

magnify; sampling time=10ms

It is successfully discretized

### Represent discrete transfer function as a difference equation (= State space representation)

H


- getDelayModel() converts transfer function to difference equation given above
- | is our voltage input | , is our voltage output

H

u | Vin y | Vout

[A,B1,B2,C1,C2,D11,D12,D21,D22,E,tau] = getDelayModel(sys)

Ref. https://www.mathworks.com/help/control/ref/ss.getdelaymodel.html

## Matlab simulation (1/2)

tau1 = 9;
sampling_time = 0.01;
s = tf('s');
G = 1/tau1*(1-exp(-tau1*s))/s;
H = c2d(G,sampling_time,'zoh'); [A,B1,B2,C1,C2,D11,D12,D21,D22,E,tau] = getDelayModel(H);
max_simulation_time = 20; %[s]
kmax = round(max_simulation_time/sampling_time); x = zeros(1,kmax);
y = zeros(1,kmax);
z = zeros(1,kmax);
w = zeros(1,kmax);
Vmax = 5; %[V]
u = Vmax*ones(1,kmax);

## Matlab simulation (2/2)

for k=1:kmax
x(k+1) = A*x(k) + B1*u(k) + B2*w(k); y(k) = C1*x(k) + D11*u(k) + D12*w(k); z(k) = C2*x(k) + D21*u(k) + D22*w(k); w(k+1) = z(max(1,k-tau));
end

t = (1:kmax)*sampling_time; subplot(211);
plot(t,u);
xlabel('Time [s]');
ylabel('Input voltage [V]');

subplot(212);
plot(t,y,'r');
xlabel('Time [s]');
ylabel('Output voltage [V]');

## Result


The digital moving average filter is successfully implemented

## Next step

- Implement the logic in Arduino (or any other MCU)
- What you need is to use the following code

for k=1:kmax
x(k+1) = A*x(k) + B1*u(k) + B2*w(k); y(k) = C1*x(k) + D11*u(k) + D12*w(k); z(k) = C2*x(k) + D21*u(k) + D22*w(k); w(k+1) = z(max(1,k-tau));
end

A = 1
B1 = 0.0100
B2 = 0
C1 = 0.1111
C2 = -0.1111
D11 = 0
D12 = 1
D21 = 0
D22 = 0
tau = 900

N.B. The loop must be run in 100[Hz] in this case

Good luck!

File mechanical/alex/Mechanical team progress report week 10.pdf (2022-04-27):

# Internship 2022


Name: ALEX MBURU

Tasks completed in the last week
- [#54]Fabrication of the motor shaft coupler
- [#54]Fabrication of the motor housing


Tasks completed in the last week
- [#54]Formulation of the vibrational isolation of the battery


Proposed alternative to the battery

# Tasks to be completed in this week

- [#31]Final assembly of the tricycle


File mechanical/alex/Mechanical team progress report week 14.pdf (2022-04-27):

# Internship 2022


Name: ALEX MBURU


Tasks completed in the last week
- [#95] Acquisition of hubs, assembly on the wheels and wheel alignment


Tasks completed in the last week
- [#94]Design and Fabrication of flanges

# Tasks to be completed in this week

[#31]Assembly of the drive train
[#31]Final assembly of the tricycle
[#90] Aesthetic finishing of E-tricycle


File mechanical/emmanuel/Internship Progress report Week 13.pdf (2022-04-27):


NAME: Emmanuel Njenga

# Tasks completed last week

## [#91] Testing the E-tricycle (test ride around the workshop

## Change of the motor housing



# Tasks in this week

### [#90] Aesthetic finishing of E-tricycle

## [#31]Fabrication and assembly of the E-tricycle

# TIMELINE

Month | Intern week | Tasks
Jan | Week 1 Week 2 | Taking measurements and 3D modelling of the tricycle Identification of parts Design of chain drive Shaft design Disassembly of the tricycle

Feb | Week 3 | Acquisition of parts Fabrication of tricycle components Literature review on E-tractors
| Week 4 | Identification of parts to be replaced on the shujaa tractor Calculation of power requirements for the shujaa tractor Measurement of chassis
| Week 5 | Design of various transmission components 3D modeling of the Shujaa tractor
| Week 6 | Vibration and stress analysis Acquisition of parts for the tricycle
March | Week 7 | Design of the transmission system of shujaa tractor Fabrication of motor shaft attachment for the tricycle Fabrication of motor housing
| Week 8 | Final fabrication of parts for the tricycle Assembly of the E-tricycle Design and acquisition of the gearbox (shujaa tractor)

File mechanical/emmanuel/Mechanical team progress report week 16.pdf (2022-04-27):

# Internship 2022


Name: Emmanuel Njenga

Tasks completed in the last week
- [#95]Brake Adjustment
- [#] Additional grab-screws on the motor shaft attachment (See video on Github)

# Tasks to be completed in this week

[#31]Final assembly of the tricycle
[#90] Aesthetic finishing of E-tricycle


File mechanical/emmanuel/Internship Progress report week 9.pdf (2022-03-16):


# Internship 2022

Name: EMMANUEL NJENGA

## Tasks completed last week


- [#31]Fabrication and assembly of the tricycle

- [#56]Design of the transmission system of the shujaa tractor From calculations the gear ratio for the two modes of operation were;
1. Working mode=47.98
2. Driving mode=17.59

The chain drive provides a gear ratio of 3.
Taking this into consideration the reduction to be provided by the gearbox in working mode is
47.98 3=15.993333

## Tasks in this week

- [#64]Acquisition of parts for the shujaa tractor

## Timeline


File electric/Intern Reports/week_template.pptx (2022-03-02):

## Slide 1

JIBEBE INTERNSHIP 2022


WEEKLY REPORT

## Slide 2

What you do with this space in the real deal


TITLE HERE


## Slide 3

TITLES HERE

What you do with this space in the real deal

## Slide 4

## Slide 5

Thank You

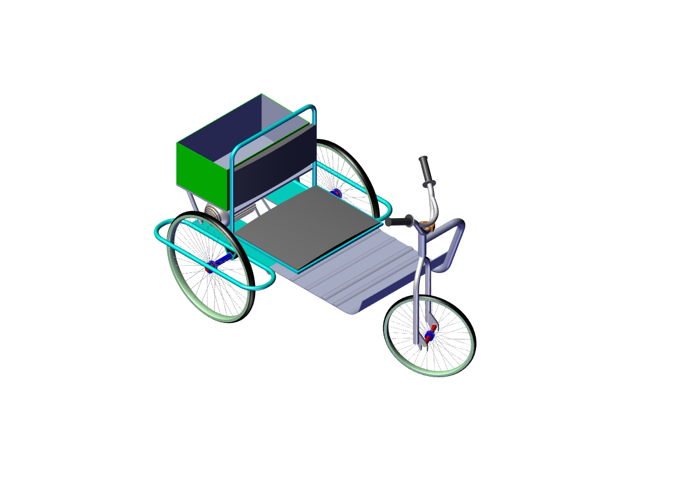
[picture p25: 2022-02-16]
mechanical/Tricycle Jibebe Project/Trycycle1.jpg

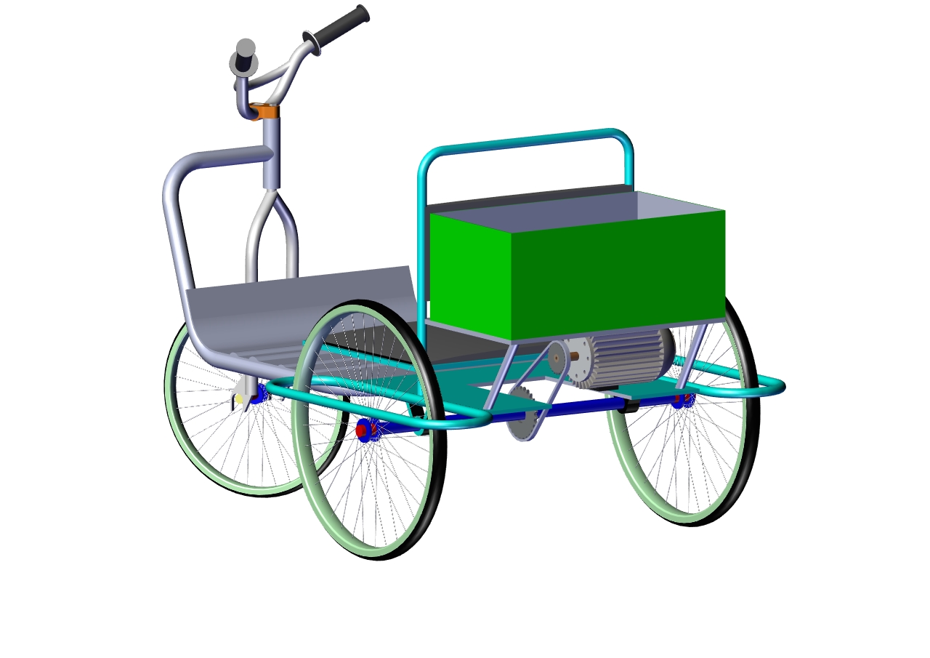
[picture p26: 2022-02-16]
mechanical/Tricycle Jibebe Project/Trycycle3.jpg

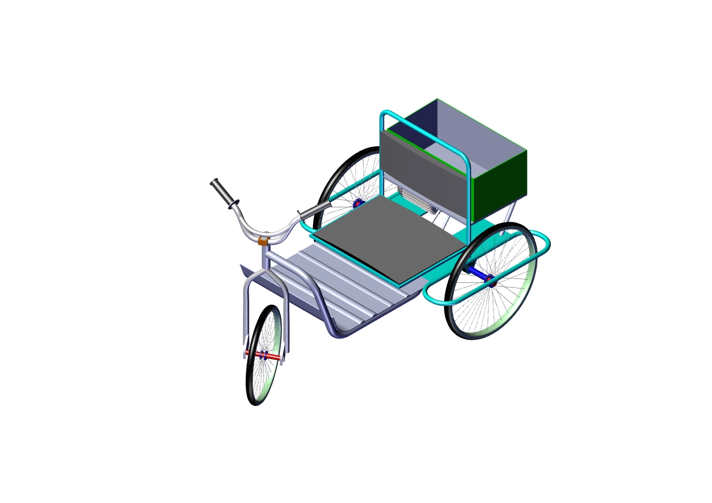
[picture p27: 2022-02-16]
mechanical/Tricycle Jibebe Project/Trycycle2.jpg

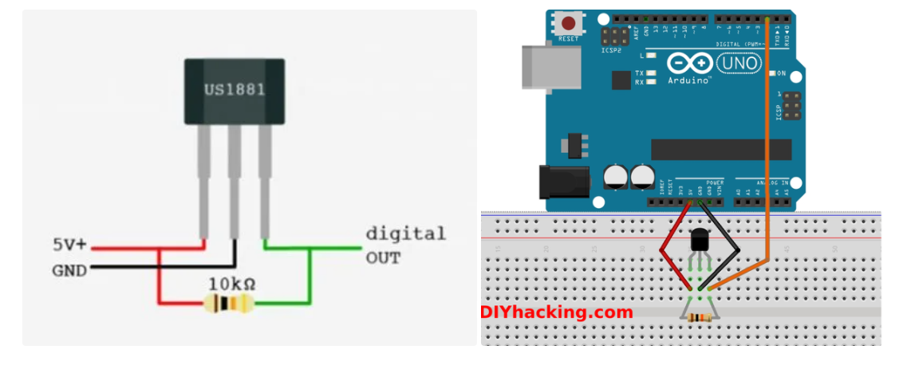
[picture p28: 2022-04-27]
electric/Research Reports/Arduino/speedomter_test/Schematic.PNG

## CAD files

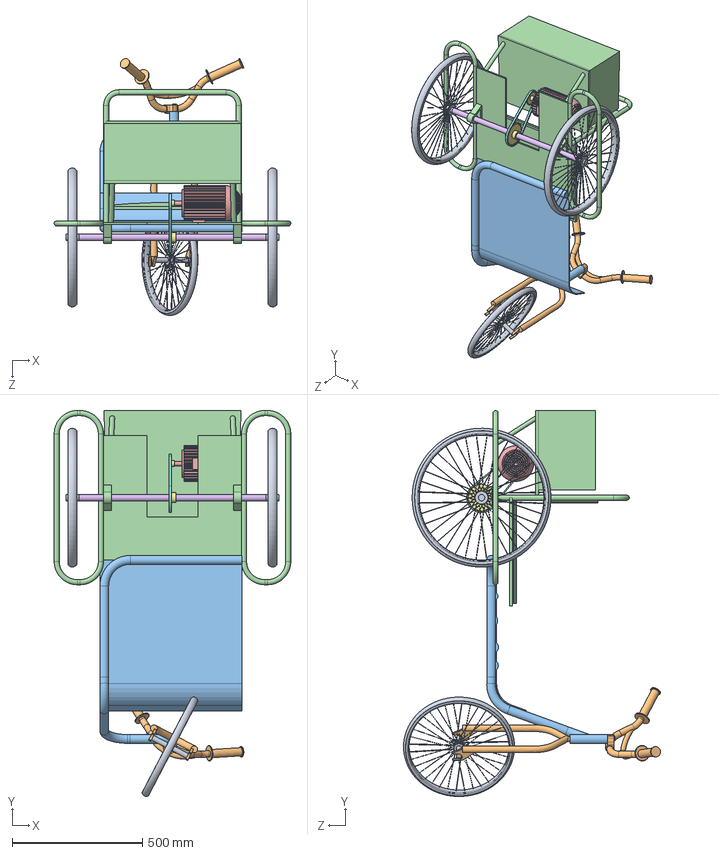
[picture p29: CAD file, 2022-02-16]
mechanical/Tricycle Jibebe Project/Trycycle.SLDASM
910.0 x 1483.7 x 988.0 mm
bicycle wheel x 3
steering
Panel
wheel guide
Elec Motor
shaft
sprocket x 2
Belt1-2^Trycycle

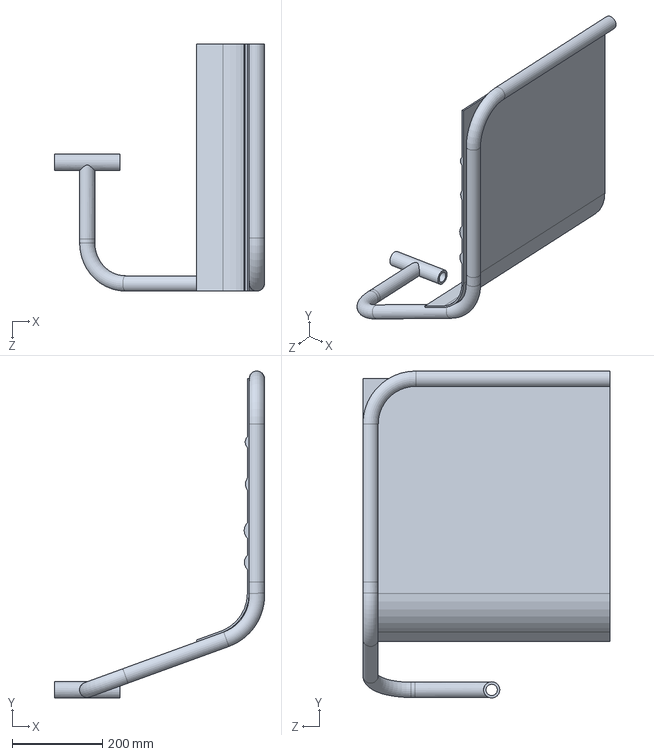
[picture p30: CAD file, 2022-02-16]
mechanical/Tricycle Jibebe Project/Panel.SLDPRT
464.9 x 723.5 x 547.0 mm

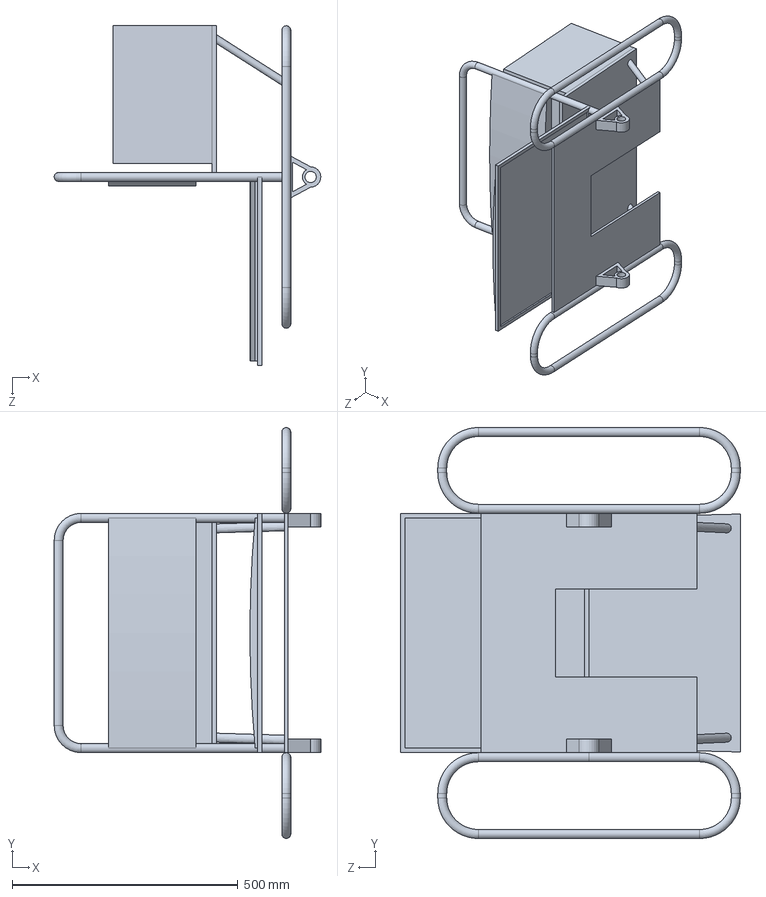
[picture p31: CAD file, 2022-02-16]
mechanical/Tricycle Jibebe Project/wheel guide.SLDPRT
590.5 x 910.0 x 752.0 mm

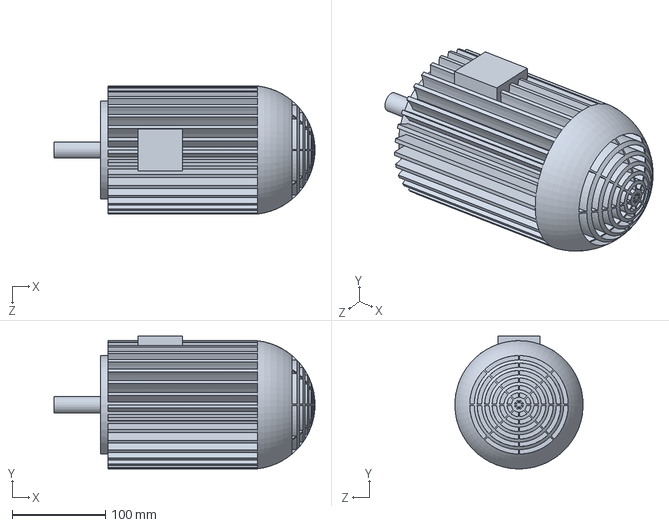
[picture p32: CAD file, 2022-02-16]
mechanical/Tricycle Jibebe Project/Elec Motor.SLDPRT
279.7 x 142.3 x 137.4 mm

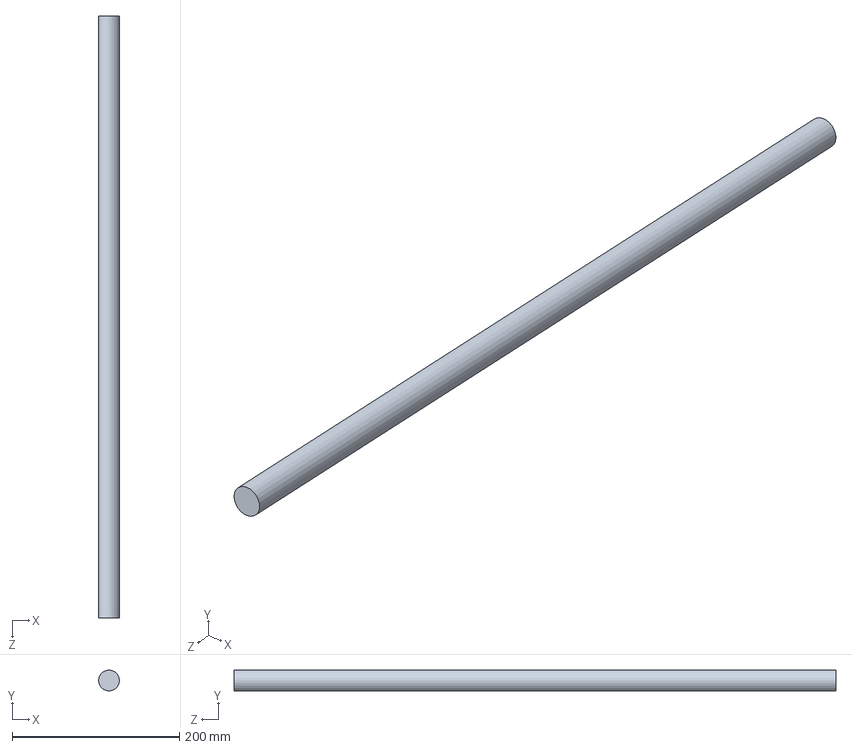
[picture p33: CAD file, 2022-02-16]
mechanical/Tricycle Jibebe Project/shaft.SLDPRT
25.0 x 25.0 x 720.0 mm

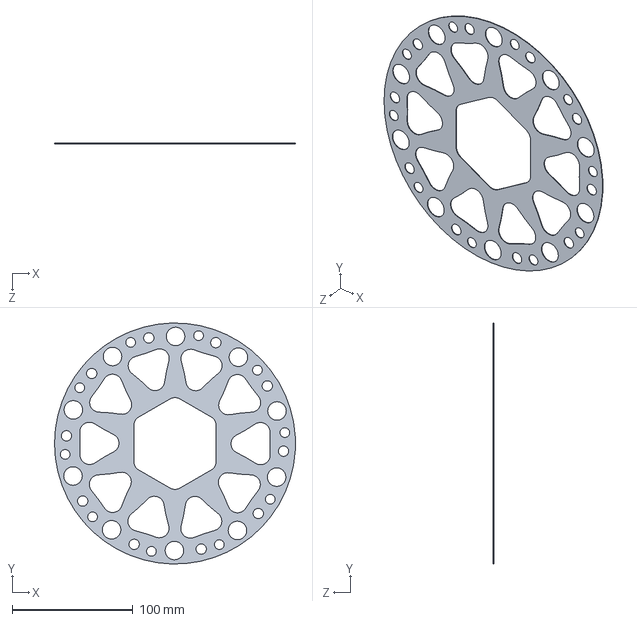
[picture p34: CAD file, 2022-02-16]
mechanical/Tricycle Jibebe Project/disc brake.SLDPRT
200.0 x 199.9 x 0.5 mm

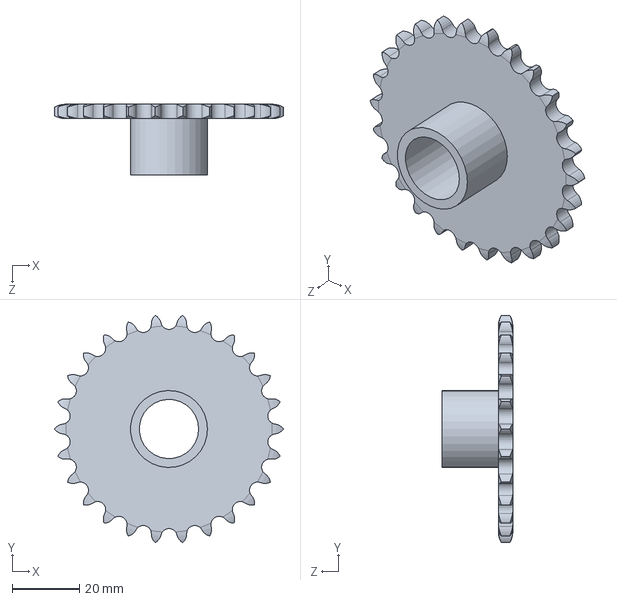
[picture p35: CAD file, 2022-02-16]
mechanical/Tricycle Jibebe Project/sprocket.SLDPRT
68.0 x 67.5 x 21.0 mm

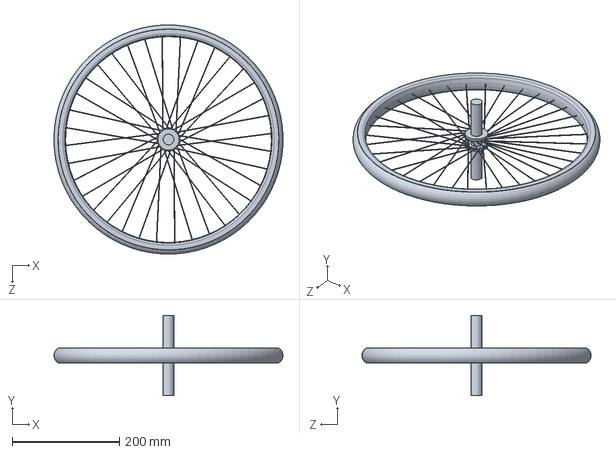
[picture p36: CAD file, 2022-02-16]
mechanical/Tricycle Jibebe Project/bicycle wheel.SLDPRT
426.8 x 150.0 x 427.1 mm

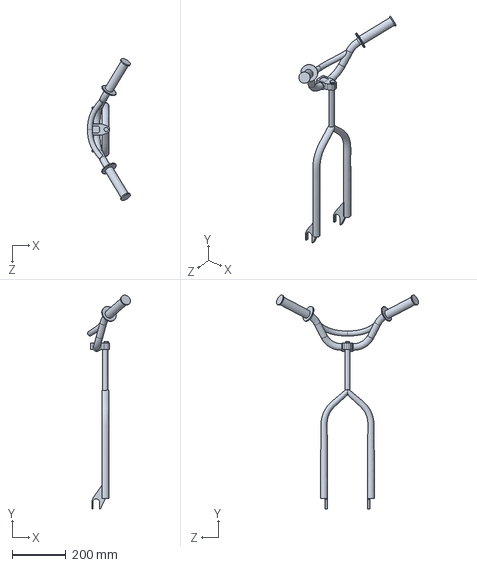
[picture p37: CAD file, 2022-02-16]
mechanical/Tricycle Jibebe Project/steering.SLDPRT
160.4 x 799.9 x 531.4 mm

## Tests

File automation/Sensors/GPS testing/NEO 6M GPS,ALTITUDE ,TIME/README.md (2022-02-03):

### Description

NEO-6M GPS Chip
The heart of the module is a NEO-6M GPS chip from u-blox. It can track up to 22 satellites on 50 channels 
and achieves the industry’s highest level of sensitivity i.e. -161 dB tracking, 
while consuming only 45mA supply current. The u-blox 6 positioning engine also boasts a Time-To-First-Fix (TTFF)
of under 1 second. One of the best features the chip provides is Power Save Mode(PSM). 
It allows a reduction in system power consumption by selectively switching parts of the receiver ON and OFF.
This dramatically reduces power consumption of the module to just 11mA making it suitable for power sensitive 
applications like GPS wristwatch. The necessary data pins of NEO-6M GPS chip are broken out to a "0.1″ pitch headers. 
This includes pins required for communication with a microcontroller over UART.

Note:- The module supports baud rate from 4800bps to 230400bps with default baud of 9600.

### Position Fix LED Indicator
There is an LED on the NEO-6M GPS Module which indicates the status of Position Fix.
It’ll blink at various rates depending on what state it’s in.

No Blinking ==> means It is searching for satellites
Blink every 1s – means Position Fix is found

### Output of sensor
Latitude,longitude, date ,time, Altitude

### Pinout
The circuit:
 * RX is digital pin 10 (connect to TX of other device)
 * TX is digital pin 1 (connect to RX of other device)

 Note:
 Not all pins on the Mega and Mega 2560 support change interrupts,
 so only the following can be used for RX:
 10, 11, 12, 13, 50, 51, 52, 53, 62, 63, 64, 65, 66, 67, 68, 69

### Power 

Note: Use 3.3V to power Vcc
GND - GND

### Library
Please install the included library

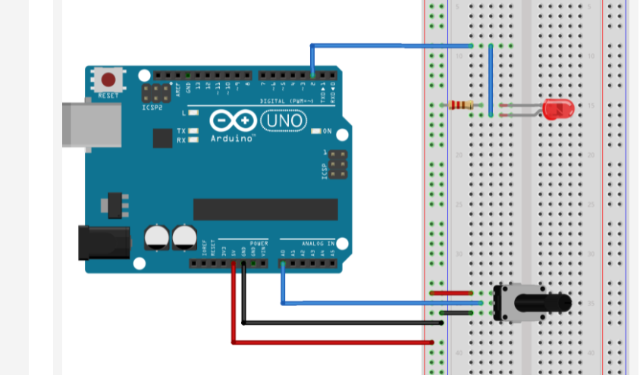
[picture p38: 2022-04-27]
electric/Research Reports/Arduino/acceleration_test/Circuit.PNG

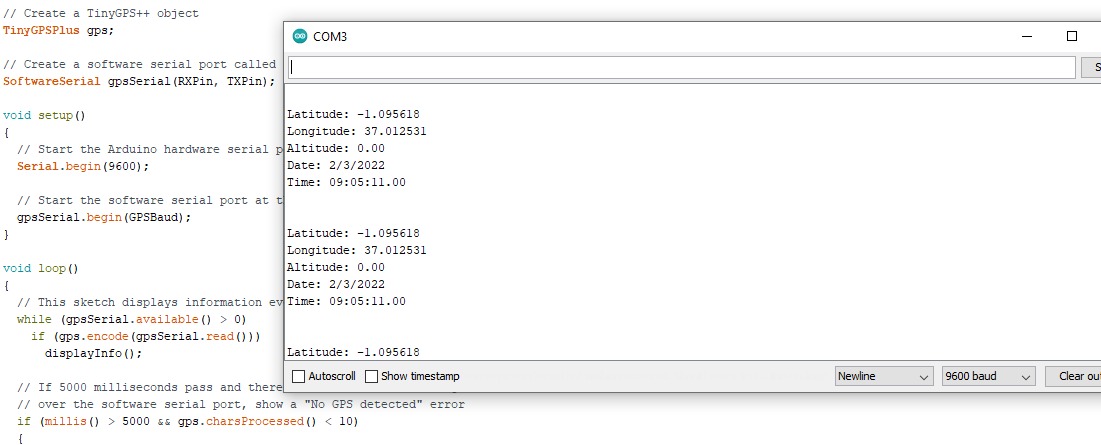
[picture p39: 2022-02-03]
automation/Sensors/GPS testing/output.jpg

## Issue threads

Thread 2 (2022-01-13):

Choice of battery

mosesmulwa-bebop, 2022-01-13:
Compare different types of batteries based on several criteria and recommend a selection

mosesmulwa-bebop, 2022-01-19:
After sizing the motor, calculations were done on the required battery size to drive the motor. The required battery pack capacity was determined to have a voltage of 48V and Ah of 50.33. This could be achieved in several ways: the most cost and weight-efficient of these methods involves using a 12V 200Ah battery and a boost converter.
The calculations can be found in the battery selection folder under the electric subsystem.
A battery selection program was also written to easily calculate the battery capacity required.

Closed 2022-01-19.

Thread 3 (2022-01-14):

Microcontroller implementation to allow for control of speed of the motor

mosesmulwa-bebop, 2022-01-14:
Involves design and implementation of mechanisms to allow for control of the speed of the motor.

mosesmulwa-bebop, 2022-01-19:
The Arduino program was implemented and speed control was able to achieved using a potentiometer. The code and schematic can be found in the speed control subdirectory.

However, because of the controller we had, there turned out to be a ready-made solution using a handlebar throttle switch that pairs with the controller we had.
It also has the added advantage of having a LED speed display eliminating the need for a separate LCD display for speed.
This was chosen as the solution to use.

## Pictures of the Handlebar Throttle Switch

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

Closed 2022-01-19.

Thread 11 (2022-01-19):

Mechanism for starting motor

gich2009, 2022-01-19:
The motor should be started at no load to eliminate the problem of very high starting torque and the load should be connected only when the torque achieves its steady state value.

Closed 2022-01-26.

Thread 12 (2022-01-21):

Motor Sizing for tricycle

gich2009, 2022-01-21:
Determination of the correct motor rating required for the tricycle load. A large motor would operate at a very low efficiency whereas a small motor would not be able to sustain the required load. Hence, the motor should be sized as close as possible to the load requirement.

Closed 2022-01-26.

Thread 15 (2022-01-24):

Redesign of the chassis drawing

Allan-2030, 2022-01-24:
Redesigning the chassis drawing so as to have dimension tolerance  for good printing

Closed 2022-02-07.

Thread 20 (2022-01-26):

Shaft design

alexmburu22, 2022-01-26:
Using the motor parameters i.e power and rated speed the diameter of the shaft is determined

alexmburu22, 2022-02-01:
Taking into consideration that the shaft is subjected to both torque and bending moment ,the shaft diameter was obtained as 16mm having taken into account a factor of safety of 1.5 using mild steel.

Closed 2022-02-01.

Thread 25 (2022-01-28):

obstacle avoidance using ultrasonic sensor

Allan-2030, 2022-01-28:

Closed 2022-02-07.

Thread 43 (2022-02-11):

Torque calculation for the e-tricycle tractor

gich2009, 2022-02-11:
The essence of these calculations is to determine whether the motor is suitable to operate in some high torque real life situations such as going up a ramp.

gich2009, 2022-02-11:
This issue was closed and the report containing the calculations is in the electric sub-repo.

gich2009, 2022-02-11:
It was established that the chosen motor could provide a sufficient torque. The calculations report for this issue is in the electric sub-repo

Closed 2022-02-11.

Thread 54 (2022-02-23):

fabrication of motor shaft attachment

emmanuelnjenga, 2022-02-23:
To couple the driving splined sprocket to the geared motor shaft a single shaft has to be designed to serve as an attachment

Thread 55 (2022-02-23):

Fabrication of the the motor housing

emmanuelnjenga, 2022-02-23:
To support the vibrating motor in position on the tricycle a house has to be made for it and welded onto the tricycle

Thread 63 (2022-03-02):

Vibrational analysis of the chassis

alexmburu22, 2022-03-02:

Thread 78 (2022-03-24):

Automatic draft control for the tractor

mosesmulwa-bebop, 2022-03-24:
Limit maximum current that can be drawn by the motor.
This should be done by use of a current sensor that detects the current drawn.
If current draw is too high:
1. If plough has been lowered,this may be the cause so immediately raise it. Some sort of solenoid valve can be used
2.  If plough is not lowered, something is wrong at the wheel.Either stuck somewhere or too much load. Thus immediately shut off the motor.
Have some sort of error code to display to the user about what has happened

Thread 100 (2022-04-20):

Acquisition of Push Button and industrial LED for Reverse Display

mosesmulwa-bebop, 2022-04-20:

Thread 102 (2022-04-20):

Design of 3D printed Hub to hold LCD, LED and Buttons for Reverse.

mosesmulwa-bebop, 2022-04-20:

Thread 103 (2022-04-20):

Development of a circuit for operating the tricycle in reverse mode

gich2009, 2022-04-20:
A circuit capable of reversing the direction of the tricycle was necessary.

Closed 2022-04-20.

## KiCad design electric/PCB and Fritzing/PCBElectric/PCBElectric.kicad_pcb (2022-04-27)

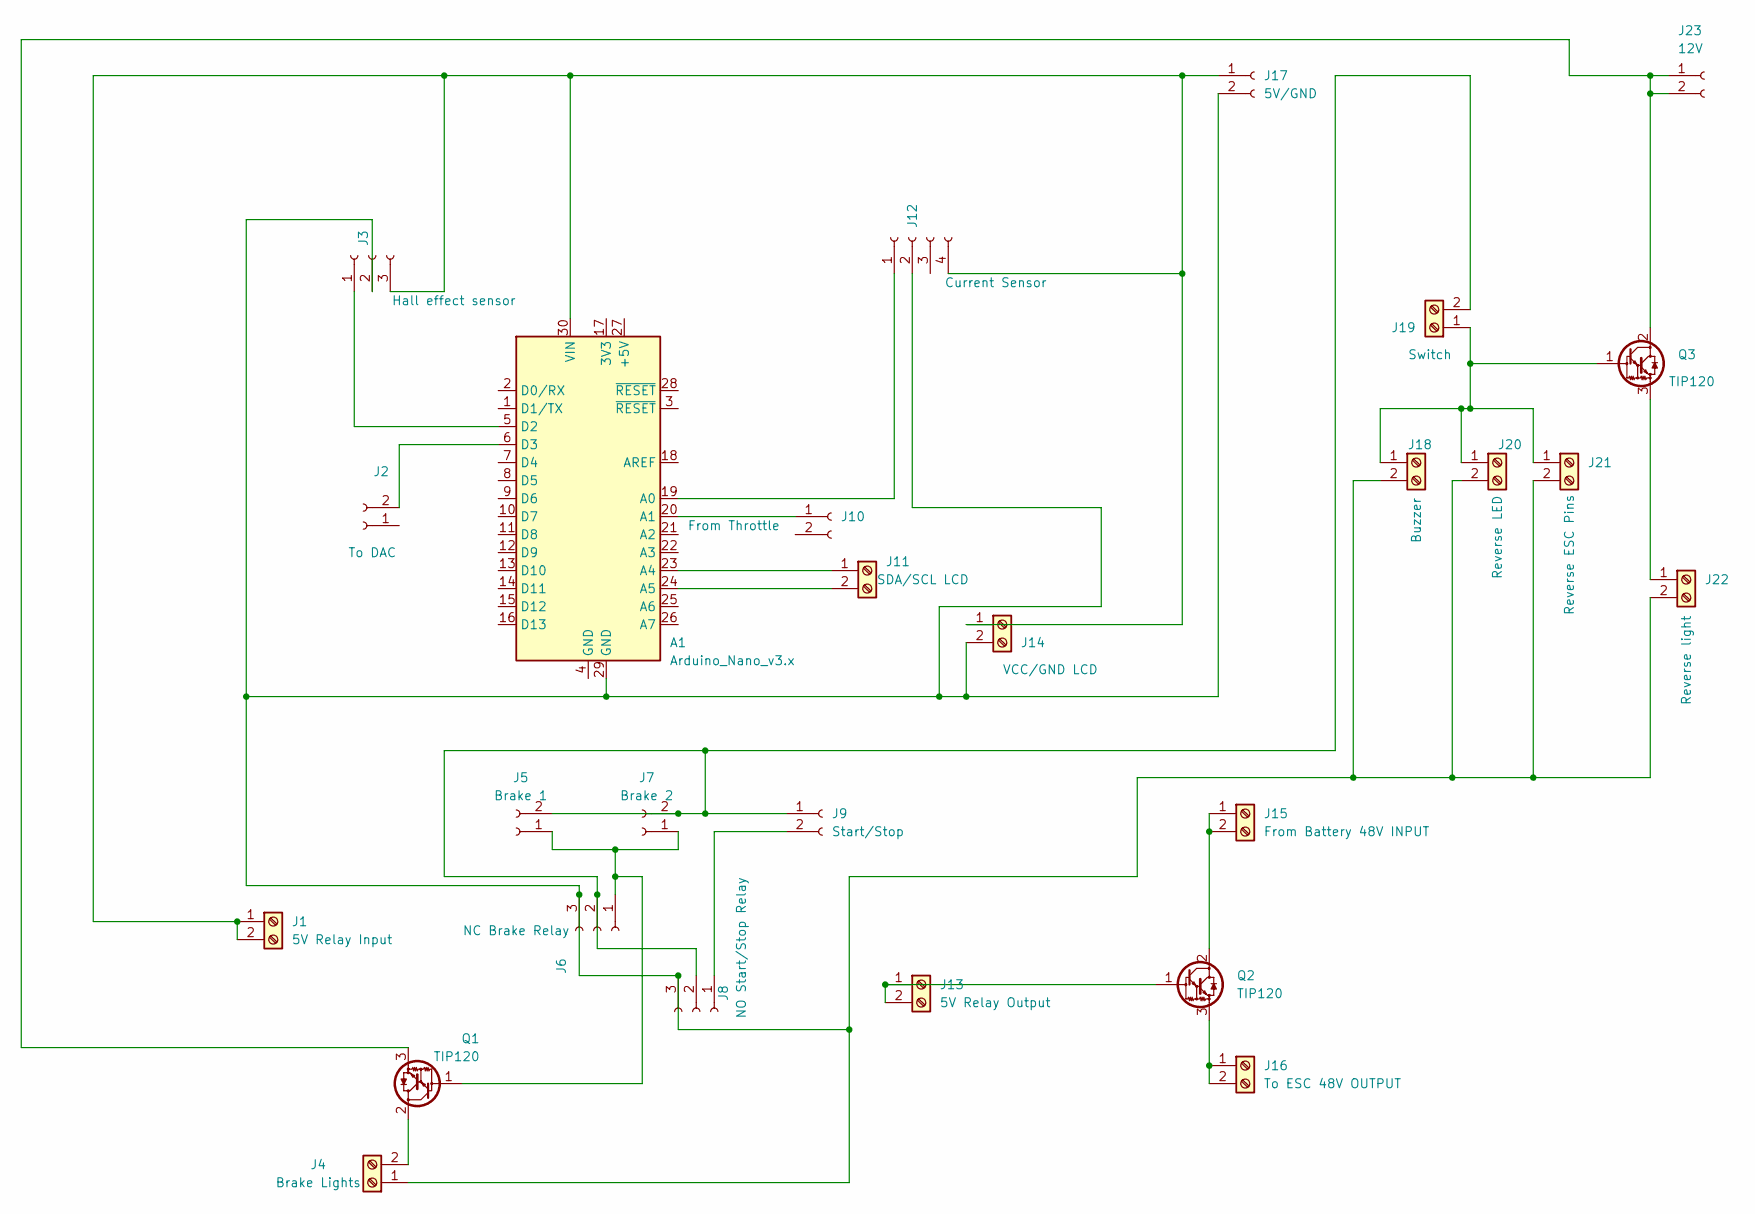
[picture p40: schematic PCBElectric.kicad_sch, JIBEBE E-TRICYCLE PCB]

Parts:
A1: Arduino_Nano_v3.x; Arduino_Nano
J1: 5V Relay Input; TerminalBlock_Altech_AK300-2_P5.00mm
J2: To DAC; PinHeader_1x02_P2.54mm_Vertical
J3: Hall effect sensor; PinSocket_1x03_P2.54mm_Vertical
J4: Brake Lights; TerminalBlock_Altech_AK300-2_P5.00mm
J5: Brake 1; PinSocket_1x02_P2.54mm_Vertical
J6: NC Brake Relay; PinSocket_1x03_P2.54mm_Vertical
J7: Brake 2; PinSocket_1x02_P2.54mm_Vertical
J8: NO Start/Stop Relay; PinSocket_1x03_P2.54mm_Vertical
J9: Start/Stop; PinSocket_1x02_P2.54mm_Vertical
J10: From Throttle; PinHeader_1x02_P2.54mm_Vertical
J11: SDA/SCL LCD; TerminalBlock_Altech_AK300-2_P5.00mm
J12: Current Sensor; PinSocket_1x04_P2.54mm_Vertical
J13: 5V Relay Output; TerminalBlock_Altech_AK300-2_P5.00mm
J14: VCC/GND LCD; TerminalBlock_Altech_AK300-2_P5.00mm
J15: From Battery 48V INPUT; TerminalBlock_Altech_AK300-2_P5.00mm
J16: To ESC 48V OUTPUT; TerminalBlock_Altech_AK300-2_P5.00mm
J17: 5V/GND; PinHeader_1x02_P2.54mm_Vertical
J18: Buzzer; TerminalBlock_Altech_AK300-2_P5.00mm
J19: Switch; TerminalBlock_Altech_AK300-2_P5.00mm
J20: Reverse LED; TerminalBlock_Altech_AK300-2_P5.00mm
J21: Reverse ESC Pins; TerminalBlock_Altech_AK300-2_P5.00mm
J22: Reverse light; TerminalBlock_Altech_AK300-2_P5.00mm
J23: 12V; PinHeader_1x02_P2.54mm_Vertical
Q1, Q2, Q3: TIP120; TO-220-3_Vertical

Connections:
unnamed: A1.5 (D2), J3.1
unnamed: A1.6 (D3), J2.2
unnamed: A1.19 (A0), J12.1
unnamed: A1.20 (A1), J10.1
unnamed: A1.23 (A4), J11.1
unnamed: A1.24 (A5), J11.2
unnamed: A1.29 (GND), J3.2, J4.1, J6.3, J8.3, J12.2, J14.2, J17.2, J18.2, J20.2, J21.2, J22.2
unnamed: A1.30 (VIN), J1.1, J1.2, J3.3, J12.4, J14.1, J17.1
unnamed: J4.2, Q1.2 (C)
unnamed: J5.1, J6.1, J7.1, Q1.1 (B)
unnamed: J8.1, J9.2
unnamed: J13.1, J13.2, Q2.1 (B)
unnamed: J15.1, J15.2, Q2.2 (C)
unnamed: J16.1, J16.2, Q2.3 (E)
unnamed: J18.1, J19.1, J20.1, J21.1, Q3.1 (B)
unnamed: J5.2, J6.2, J7.2, J8.2, J9.1, J19.2
unnamed: J22.1, Q3.3 (E)
unnamed: J23.1, J23.2, Q1.3 (E), Q3.2 (C)

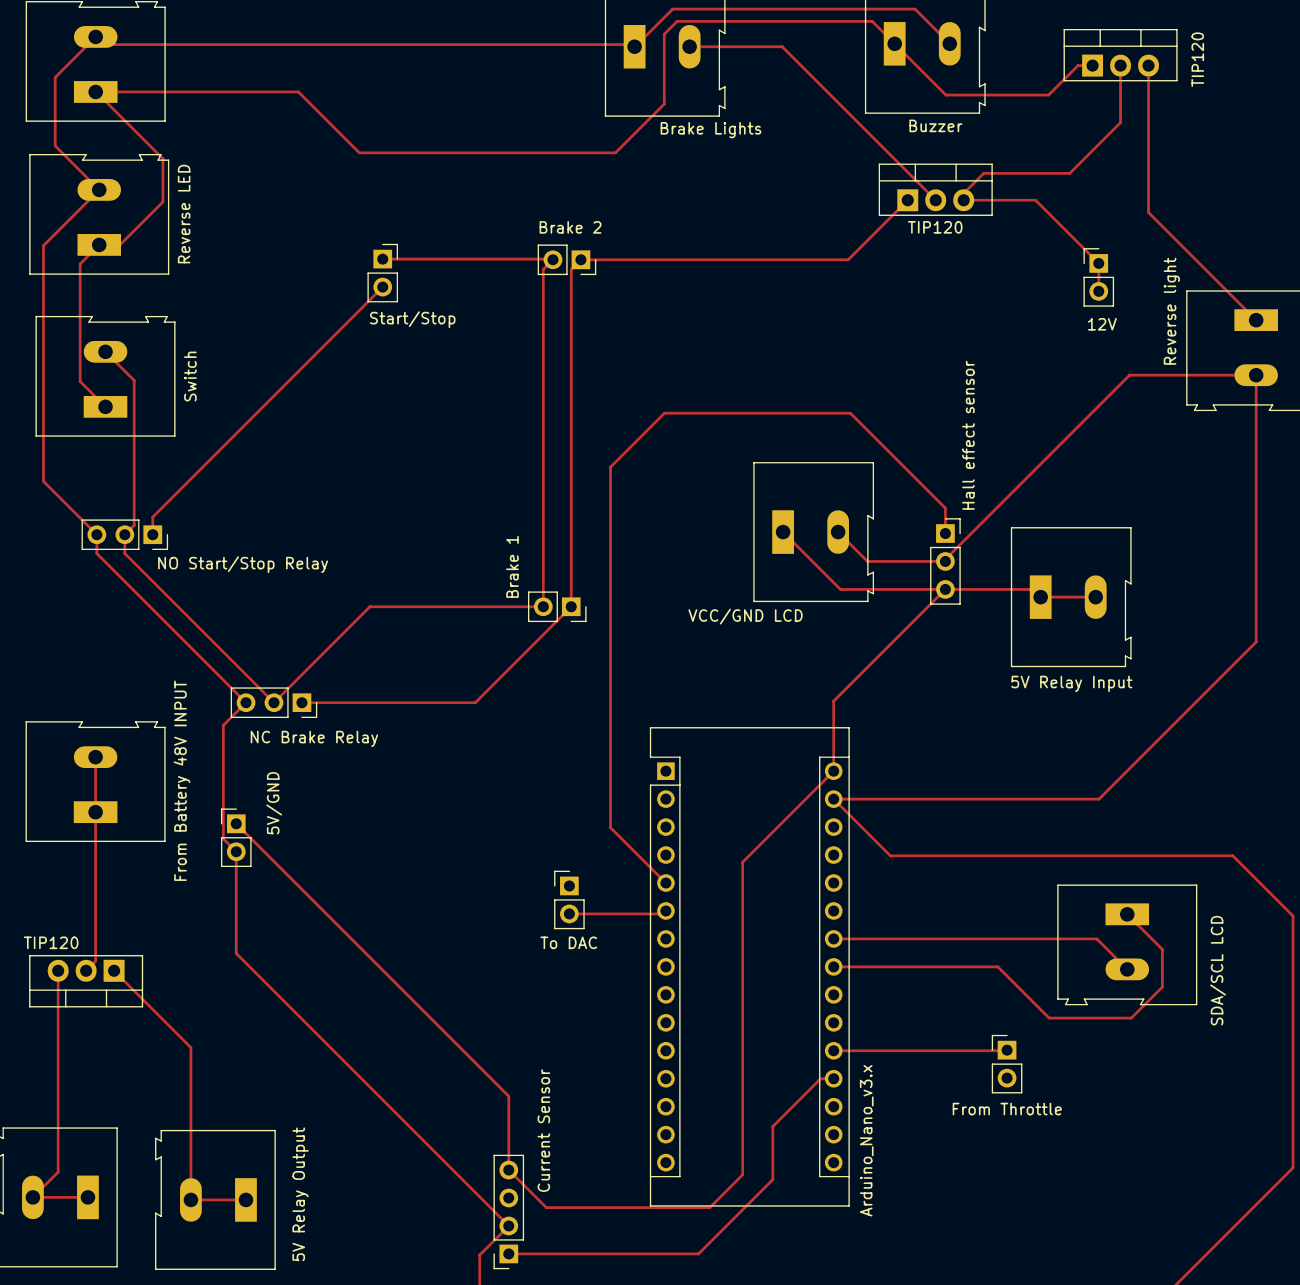
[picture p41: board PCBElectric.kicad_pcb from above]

Board: 2 copper layers, 27 parts (0 on the bottom side), 18 nets.

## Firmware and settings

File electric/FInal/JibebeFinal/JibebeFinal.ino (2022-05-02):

/*
 * 
 * Jibebe Final
The Final Code for the Jibebe Tricycle Electrical Susbsystem.

Jibebe Github: https://jibebe-jkuat.github.io/

Authors:
Paul Moses - Computer Engineer
Amos Wanene - Electrical Engineer
Brian Willy - Electrical Engineer


Board to be used: Arduino Due
Functions of the Code:
*******1. Speed and Throttle Control for BLDC Motor

Throttle ----------------------> Arduino -------------------> Motor Speed Controller
Uses inbuilt ADC to read throttle value and uses DAC to write analog value to Speed Controller 

Input -------> throttle Value
Output -----> Corrected Speed Value

Functions used: readThrottle and writeSpeed

*******2. Battery Percentage Determination
*
Uses Current Sensors and coloumb counting algorithm to calculate the battery Percentage.
Input ----> Currrent Sensor Value
Output ----> Battery Percentage

This fucntion controls the value of the battery Percentage variable

*****3. Velocity Determination
*
*Uses Stationary Hall Sensor and rotating magnet to determine the speed of the rotating wheel of the tricyle

Input ------> Hall Sensor Trips by Magnet
Output -----> Speed in km/h

Functions : calculateVelocity
Controls the speed_km_h_value variable

*****4. Speed and Battery percentage display on LCD

Input ---> Battery percentage and Speed derived from previous functions
Output ---> Display values and text describing them to an LCD.
*/

///----------------------------------------PIN ASSIGNMENTS-----------------------------//
int hall_sensor_pin = 2; //digital pin 2
//-------------------------------------------------------------------------------------//

//-----------------------------------------VELOCITY DETERMINATION INITS----------------//
// set number of hall trips for RPM reading (higher improves accuracy)
//100
float hall_thresh = 10.0;
float wheel_diameter = 0.6; // in meters
float speed_km_h_value = 0.0;
//------------------------------------------------------------------------------------//

//-----------------------------------BATTERY PERCENTAGE INITS-------------------------//
int battery_percentage = 0;
float         offsetVoltage = 2539.062;
int           currentPin = A1;
int           singleValue, adcValue, rawSensorValue;
float         sensitivity = 33;
float         currentValue, adcVoltage, samples;
unsigned long startMillis;  //some global variables available anywhere in the program
unsigned long currentMillis;
const int     period = 1000;  //the value is a number of milliseconds
const byte    ledPin = 13;    //using the built in LED
double        totalCoulombs = 0.0;
const int     capacity = 48;

//-----------------------------------------------------------------------------------//

//-----------------------------------SPEED CONTROL INITS----------------------------//
int speedOutput = DAC1;
int  checkValue, midValue, x, prevValue = 0;
float currentPotVal;
int throttle = A0;
//---------------------------------------------------------------------------------//

//---------------------------------------LCD INITS-----------------------------------//
#include <Wire.h> 
#include <LiquidCrystal_I2C.h>

LiquidCrystal_I2C lcd(0x27,16,2);  // set the LCD address to 0x27 for a 16 chars and 2 line display
//-----------------------------------------------------------------------------------//



void setup() {
  // initialize serial communication at 9600 bits per second:
  Serial.begin(9600);

  //------HALL SENSOR
  pinMode(hall_sensor_pin, INPUT); // make the hall sensor pin an input

  //-----LCD 
  lcd.init();  
  lcd.backlight();

  //---SPEED CONTROL
  analogWriteResolution(8);

  //---BATTERY
  pinMode (currentPin, INPUT);
  startMillis = millis();  //initial start time
  

}




void loop() {
  //calculate Velocity
  speed_km_h_value = calculateVelocity();
  battery_percentage = calculateBattPercentage();
  lcdDisplayBattAndSpeed(battery_percentage,speed_km_h_value);
  speedControl();
  delay(1);
  
}


/*-------------------------------------------------------------CALCULATE BATTERY PERCENTAGE ------------------------------------------------------**/

float calculateBattPercentage(){
  adcValue = readAnalog(currentPin);
  adcVoltage   = (adcValue / 1024.0) * 5000;
  currentValue = ((adcVoltage - offsetVoltage) / sensitivity);
  int batt_percentage =   getCoulombs(currentValue);;
  return batt_percentage;
}


int getCoulombs(float current)
{
  currentMillis = millis();  //get the current "time" (actually the number of milliseconds since the program started)
  if ( (currentMillis - startMillis) < period){  //test whether the period has elapsed, if not, return.
    return -1;
  }
  
    totalCoulombs = totalCoulombs + current;
    float usedCoulombs = totalCoulombs/3600.0;
    startMillis = currentMillis;  //IMPORTANT to save the start time of the current LED state.
    float batt_per =   ((capacity - usedCoulombs) / capacity) * 100;
    return batt_per;

   
}
/*------------------------------------------------------------CALCULATE VELOCITY--------------------------------------------------------------*/
float calculateVelocity(){
  /*Calculate velocity from number of hall sensor trips and returns velocity in km/h*/
  
  // preallocate values for tach
  float hall_count = 1.0;
  float start = micros();
  bool on_state = false;
  // counting number of times the hall sensor is tripped
  // but without double counting during the same trip
  while(true){
    if (digitalRead(hall_sensor_pin)==0){
      if (on_state==false){
        on_state = true;
        hall_count+=1.0;
      }
    } else{
      on_state = false;
    }
    
    if (hall_count>=hall_thresh){
      break;
    }
  }
  
  // print information about Time and RPM
  float end_time = micros();
  float time_passed = ((end_time-start)/1000000.0);
  //Serial.print("Time Passed: ");
  //Serial.print(time_passed);
  //Serial.println("s");
  float rpm_val = (hall_count/time_passed)*60.0;
  //Serial.print(rpm_val);
  //Serial.println(" RPM");
  float speed_km_h = 0.1885 * rpm_val * wheel_diameter; 
  //Serial.print(speed_km_h);
 // Serial.println(" KM/H");
  //delay(1);        // delay in between reads for stability
  return speed_km_h;
}

/**-------------------------------------------------------------SPEED CONTROL-----------------------------------------------------------------**/
int readAnalog(int analogPin){
  samples = 0.0;

  for (int i = 0; i < 10; i++){          //Get 10 samples
     singleValue = analogRead(analogPin);     //Read current sensor values
     samples += singleValue;        //Add samples together
     }
    
    singleValue = samples / 10;
    singleValue = map (singleValue, 0, 1023, 0, 255);
    return singleValue;
}

void speedControl(){
  currentValue = readAnalog(throttle);

    if (currentValue != prevValue){
      if (prevValue < currentValue){
        for (x = prevValue; x < currentValue; x++){          //Get 10 samples
          checkValue = readAnalog(throttle);
          if (checkValue != currentValue){
            break;
          }
          analogWrite(speedOutput, x) ;     
        }
      }

      if (prevValue > currentValue){
        for (x = currentValue; x > prevValue; x--){          //Get 10 samples
          checkValue = readAnalog(throttle);
          if (abs (checkValue != currentValue)){
            break;
          }
          analogWrite(speedOutput, x) ;     
        }
      }
     prevValue = currentValue;
    }
  
}



/*--------------------------------------------------------------LCD DISPLAY--------------------------------------------------------------------------------------*/
void lcdDisplayBattAndSpeed(int battery_percentage, float speed_km_h){
  String batStr = "BATTERY: ";
  String speedStr = "KM/H: ";

  String final_bat_str = batStr + battery_percentage;
  String final_speed_str = speedStr + speed_km_h;

  if (battery_percentage != -1){
    lcd.setCursor(0,0); //topLeft
    lcd.print(final_bat_str);
  }
  
  lcd.setCursor(0,1);//bottomLeft
  lcd.print(final_speed_str);
  
}

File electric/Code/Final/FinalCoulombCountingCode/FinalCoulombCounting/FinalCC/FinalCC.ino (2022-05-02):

//float       offsetVoltage = 2163.086;
float         offsetVoltage = 2539.062;
int           currentPin = A0;
int           singleValue, adcValue, rawSensorValue;
float         sensitivity = 33;
float         currentValue, adcVoltage, samples;
unsigned long startMillis;  //some global variables available anywhere in the program
unsigned long currentMillis;
const int     period = 1000;  //the value is a number of milliseconds
const byte    ledPin = 13;    //using the built in LED
double        totalCoulombs = 0.0;
void          getCoulombs (float current);
const int     capacity = 48;

void setup(){
  Serial.begin(9600);
  pinMode (currentPin, INPUT);
  startMillis = millis();  //initial start time
}


void loop(){
samples = 0.0;
  for (int x = 0; x < 200; ++x){ //Get 190 samples
  singleValue = analogRead(currentPin);     //Read current sensor values   
  samples     = samples + singleValue;  //Add samples together
  delay (5); // let ADC settle before next sample 5ms
}

  adcValue     = samples / 200.0;
  adcVoltage   = (adcValue / 1024.0) * 5000;
  currentValue = ((adcVoltage - offsetVoltage) / sensitivity);
 
  Serial.print("Raw Sensor Value = " );
  Serial.print(adcValue);
  //delay(20);

  Serial.print("\t Voltage(mV) = ");
  Serial.print(adcVoltage,3);
  //delay(20);
 
  Serial.print("\t Current = ");
  Serial.println(currentValue,3);
  //delay(10);
  getCoulombs(currentValue);

}
 
int getCoulombs(float current)
{
  currentMillis = millis();  //get the current "time" (actually the number of milliseconds since the program started)
  if ( (currentMillis - startMillis) < period){  //test whether the period has elapsed, if not, return.
    return;
  }
  
    totalCoulombs = totalCoulombs + current;
    float usedCoulombs = totalCoulombs/3600.0;
    Serial.print("Total Coulombs = ");
    Serial.println(totalCoulombs);
    Serial.print("Total Ah = ");
    Serial.println(usedCoulombs);

    return (((capacity - usedCoulombs) / capacity) * 100)

    //digitalWrite(ledPin, !digitalRead(ledPin));  //if so, change the state of the LED.  Uses a neat trick to change the state
    startMillis = currentMillis;  //IMPORTANT to save the start time of the current LED state.
}

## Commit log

2022-01-14 Uploaded Schematic For Speed Control
2022-01-16 Uploaded pdf containing choice of battery
2022-01-16 Uploaded code and schematic for speed control
2022-01-17 uploaded battery selection program
2022-01-17 tractor robot chassis
2022-01-18 uploaded battery and motor sizing calculations
2022-01-19 Updated speed control
    Uploaded images of the suggested handlebar throttle switch
2022-01-19 🚀 RELEASE: Week 1 progress report
2022-01-21 Add files via upload
    First document describing the choice of battery and motor
2022-01-26 🚀 RELEASE: Week 2 progress report
2022-02-02 🚀 RELEASE: Week 3 progress report
2022-02-02 uploaded obstacle ultrasonic
2022-02-08 🚀 RELEASE: Week 4 progress report
2022-02-16 3D model
    [Elec Motor.SLDPRT, Panel.SLDPRT, Trycycle.SLDASM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]
2022-02-19 🚀 RELEASE: Week 5 progress report
2022-03-02 🚀 RELEASE: Week 7 progress report
2022-03-23 🚀 RELEASE: Week 10 progress report
2022-04-10 Create Sketch 1(has buzzer,led and reverse).fzz
    [Sketch 1(has buzzer,led and reverse).fzz]
2022-04-27 🚀 RELEASE: Week 16 progress report
